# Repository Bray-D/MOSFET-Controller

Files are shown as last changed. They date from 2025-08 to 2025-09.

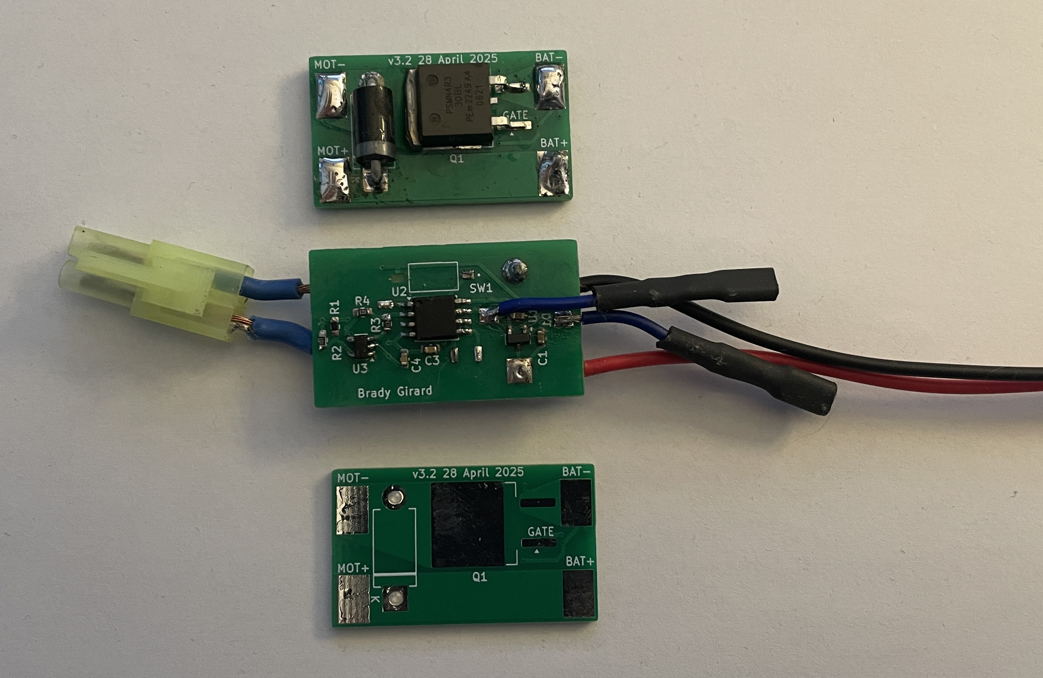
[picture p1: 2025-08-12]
hardware/IMG_0932.JPG

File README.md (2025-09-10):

# MOSFET-Controller
This repository contains all relevant files for my custom MOSFET controller. It includes hardware designs,
schematics, and code. This project is solely developed by Brady Girard. 

If anyone reads this, thank you for looking at my projects. I make them for niche personal uses, but they let me
learn new things and improve my electronics skills.

# Purpose
The purpose of this project was to control a DC motor using a MOSFET and microcontroller (MCU). The MCU
interrupts power flow to the motor to control the number of revolutions. It does not control the speed of
the motor. This project is applicable to, but not limited to, small pump controls, solenoid driving, 
remote-controlled devices, and DC motor control.

# Implementation
The MCU currently used is an ATtiny85. It works by staying in sleep mode until the trigger signal is detected, where it 
wakes and proceeds to one of two scenarios:
1. Start the motor, and count milliseconds until desired time is reached. This allows for precise revolution control.
2. Start the motor, and keep rotating until trigger signal goes inactive. (Acts like a buffer)

The MOSFET was not driven directly from the ATtiny85, as this could damage it. Instead, a MOSFET driver chip was used.
This allows for a higher power MOSFET to be driven, from the same MCU. It was desired to keep the PCB size small, as the
space restriction was tight. However, a bigger circuit board will allow for a more powerful MCU (STM32, ESP32, etc),
higher power FETs, and higher continuous current flow.
For a bill of materials, see the [hardware folder](/hardware). This folder also contains the schematics and layouts.

# Electrical Characteristics
- The controller works with batteries from 6V to 20V. Any voltage higher than 20V will damage the MOSFET.
Any voltage lower than 6V will not power the MCU correctly. 
- In low power mode, current draw is 300 uA.
- Two wire input (one ground, one trigger) allows for stable triggering and external ground reference.
- Wakeup voltage should not exceed 5V. At least 4V is recommended for stability.
- Input signal wakes MCU on falling edge.
- High power design allows PCB to withstand 15A of continuous current.
- Able to withstand ~25A of peak current during motor startup.
- Programmed through SPI.
(Any in depth characteristics should be taken from the ATtiny85 datasheet.)

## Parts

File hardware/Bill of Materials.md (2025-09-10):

# Bill of Materials

|Designator|Value|Footprint|Quantity|
|-----|-----|-----|-----|
|C1, C2|1μF|0603 (1608 Metric)|2|
|C3, C4|100nF|0603 (1608 Metric)|2|
|D1|STPS3150RL|DO201AD|1|
|Q1|PSMN4R3-30BL|D2PAK|1|
|R1|47Ω|0603 (1608 Metric)|1|
|R2, R4|10kΩ|0603 (1608 Metric)|2|
|R3|470Ω|0603 (1608 Metric)|1|
|SW1|DIP SPST|[datasheet](https://www.sameskydevices.com/product/resource/ds04-254-smt.pdf)|1|
|U1|MCP1799T|SOT23-3|1|
|U2|ATtiny85V-10S|8SOIC|1|
|U3|MCP1402T|SOT23-5|1|

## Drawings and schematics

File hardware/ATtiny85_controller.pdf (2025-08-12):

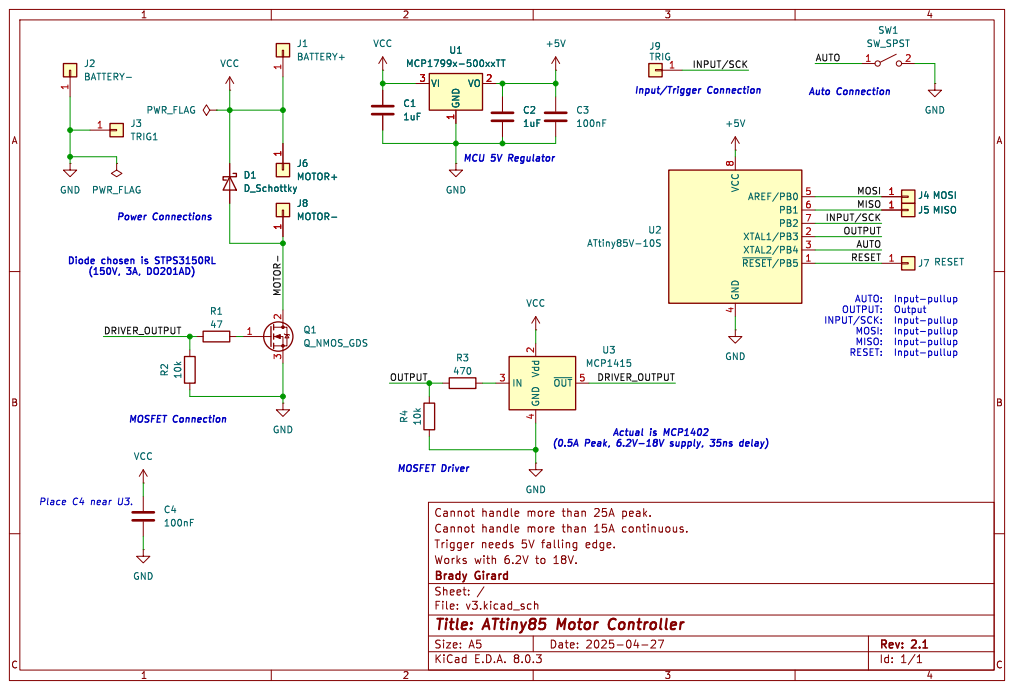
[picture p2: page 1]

INPUT/SCK: MOSI: MISO: RESET: D1 D_Schottky

INPUT/SCK DRIVER_OUTPUT Diode chosen is STPS3150RL

Input-pullup AUTO: OUTPUT:

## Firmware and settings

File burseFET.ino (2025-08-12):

#include <avr/interrupt.h>
#include <avr/sleep.h>
#include <avr/power.h>

#define TRIGGER_PIN 2     // PB2
#define OUTPUT_PIN 3      // PB3
#define AUTO_SELECT_PIN 4 // PB4

bool ready = false;
bool ignoreCycleNum = false;   // Ignore number of desired revolutions if true
int cycleTime = 87;    // Time to spin once. Measured in milliseconds
int cycleNum = 3;      // Number of desired revolutions

void setup() {
  pinMode(OUTPUT_PIN, OUTPUT);
  pinMode(TRIGGER_PIN, INPUT_PULLUP);
  pinMode(AUTO_SELECT_PIN, INPUT_PULLUP);

  // Setup other pins as INPUT_PULLUP to decrease power
  pinMode(0, INPUT_PULLUP);
  pinMode(1, INPUT_PULLUP);
  pinMode(5, INPUT_PULLUP);
}

void sleepMCU() {
  set_sleep_mode(SLEEP_MODE_PWR_DOWN);
  sleep_enable();
  attachInterrupt(0, onWake, LOW);
  
  ADCSRA &= ~ bit(ADEN); // Disable analog-digital converter to reduce power
  power_all_disable();    // Turn all peripherals off
  power_timer0_enable();  // Enable tim0 to allow interrupts

  sleep_mode(); // Go to sleep

  sleep_disable();  // Execution resumes here on wakeup
  detachInterrupt(0); // Prevent further triggers while MCU is awake
}

void onWake() {
  ready = true;
  ignoreCycleNum = !digitalRead(AUTO_SELECT_PIN);
}

void loop() {
  static int currentTime = 0;
  if (ready) {
    if (ignoreCycleNum) {
      while(digitalRead(TRIGGER_PIN) == LOW) {
        digitalWrite(OUTPUT_PIN, HIGH); // Turn on FET while input is active
      }
      digitalWrite(OUTPUT_PIN, LOW);  // Turn off fet
    } else {
      digitalWrite(OUTPUT_PIN, HIGH);
      while(digitalRead(TRIGGER_PIN) == LOW) {
        if (currentTime < cycleNum * cycleTime) { // Keep track of how many ms has past since turn on
          currentTime += 1;   // Add a ms to the count
        } else {
          digitalWrite(OUTPUT_PIN, LOW);
        }
        delay(1); // wait a ms
      }
      digitalWrite(OUTPUT_PIN, LOW);
      currentTime = 0;
    }
  }
  sleepMCU();
}

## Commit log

2025-08-12 KiCad schematic for ATtiny85 version
    [v3.kicad_sch]
2025-08-12 Update and rename v3.kicad_sch to hardware/v3.kicad_sch
    [v3.kicad_sch]
2025-08-12 Schematic for ATtiny85 in PDF form
2025-08-12 Update and rename v3.kicad_sch to ATtiny85_controller.kicad_sch
    [ATtiny85_controller.kicad_sch]
2025-08-12 Added photo of circuit board
2025-09-10 Create Bill of Materials
2025-09-10 Update Bill of Materials
2025-09-10 Rename Bill of Materials to Bill of Materials.txt
2025-09-10 Rename Bill of Materials.txt to Bill of Materials.md
2025-09-11 Added KiCad schematic of circuit board.
2025-09-11 Deleted hardware/schematic.pdf
    This file was for the wrong project.
